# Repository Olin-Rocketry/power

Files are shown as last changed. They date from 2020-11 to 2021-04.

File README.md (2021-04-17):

# Power

## Current Design 
**Two independent groups of 3 cells in series.** <br>
**Nominal voltage: 12.3V**  <br>
**Nominal current: 4000 mAh** <br>

### The 25R 18650 Li-ion Battery
- Discharge rate: 2000 mA
- Range of voltage: 3.6V (EoD) - 4.1V (EoC)
- Current rating: 2500mAh
- Max voltage (switch from CV to CC):  4.1V
- Icc (charging current) = .25 A 
- Max cycle life: 100 cycles  
- Normal capacity: 80% (assumed) 
- Temperature range: -20 - 50 C

## System Diagram 
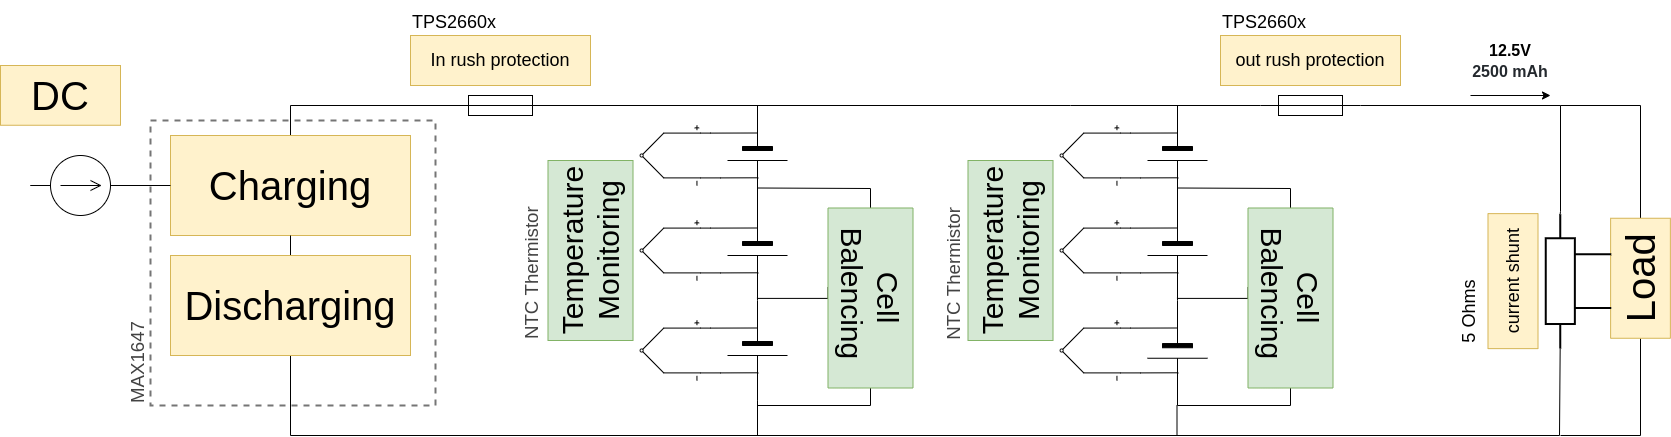
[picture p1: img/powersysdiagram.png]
bms_system_diagram


## Power Distribution
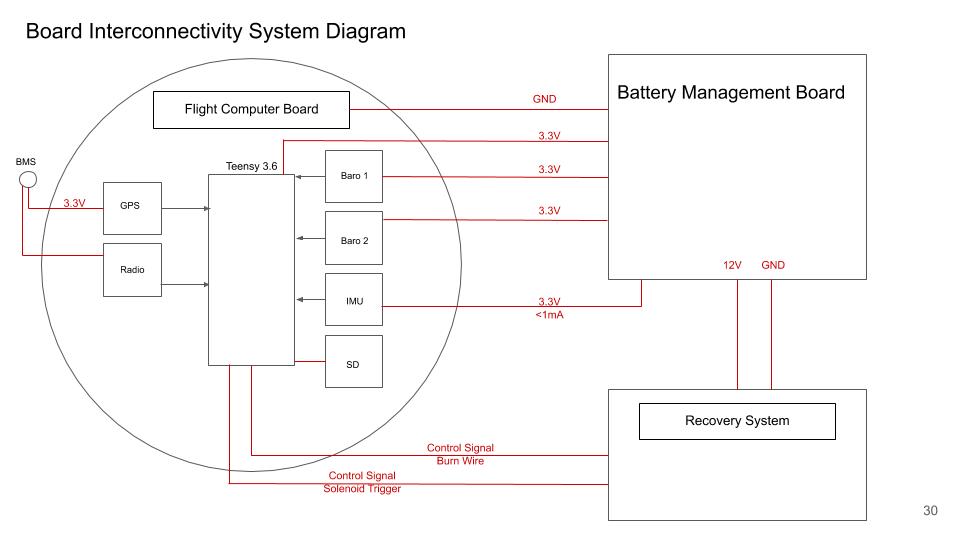
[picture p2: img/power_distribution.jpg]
power distribution


## Rev1 Schematic *1/2021
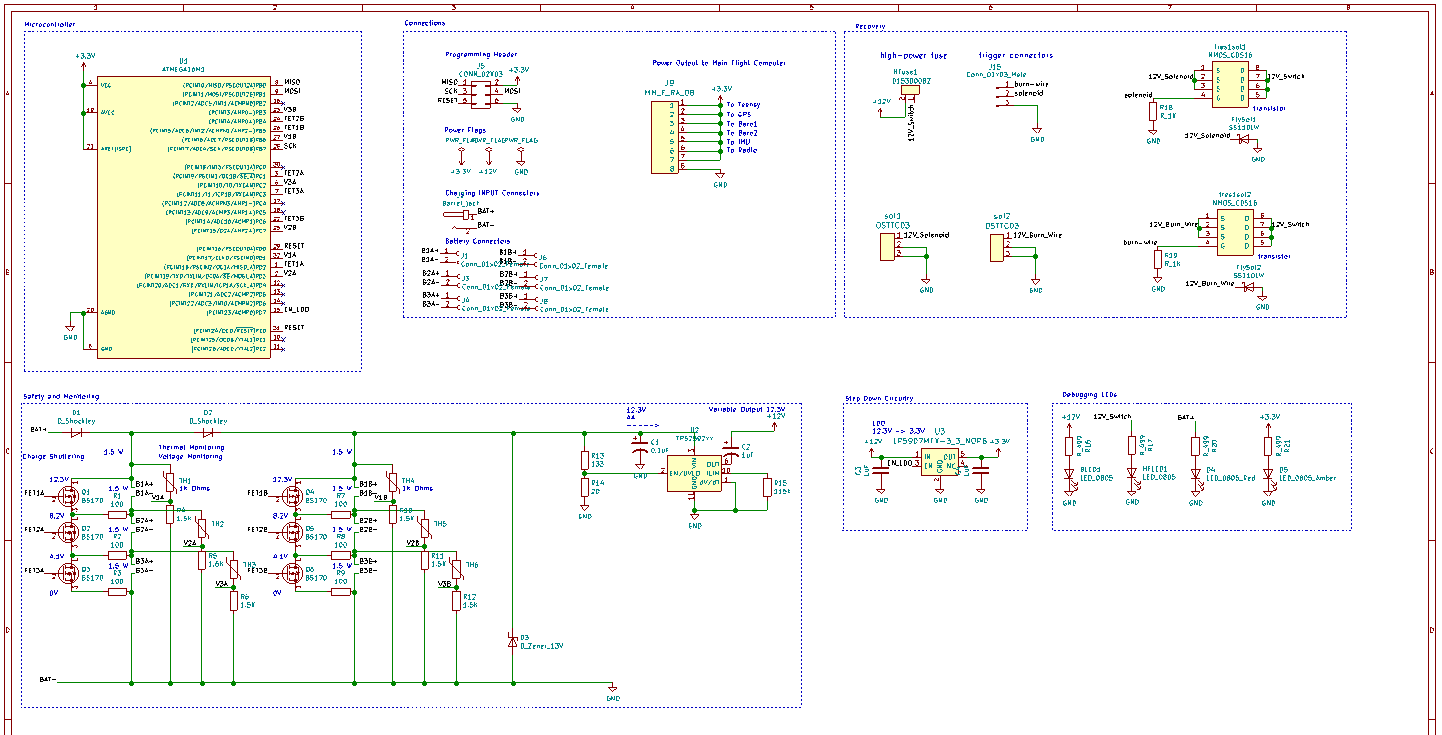
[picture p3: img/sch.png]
rev1_sch


## Rev1 PCB Layout and 3D Model *1/2021
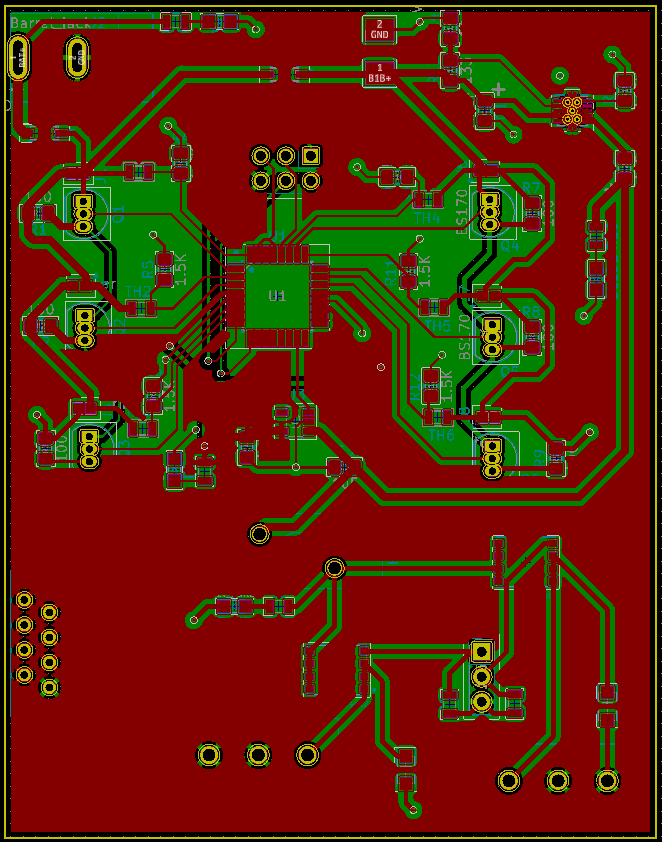
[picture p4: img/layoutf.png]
rev1_layout
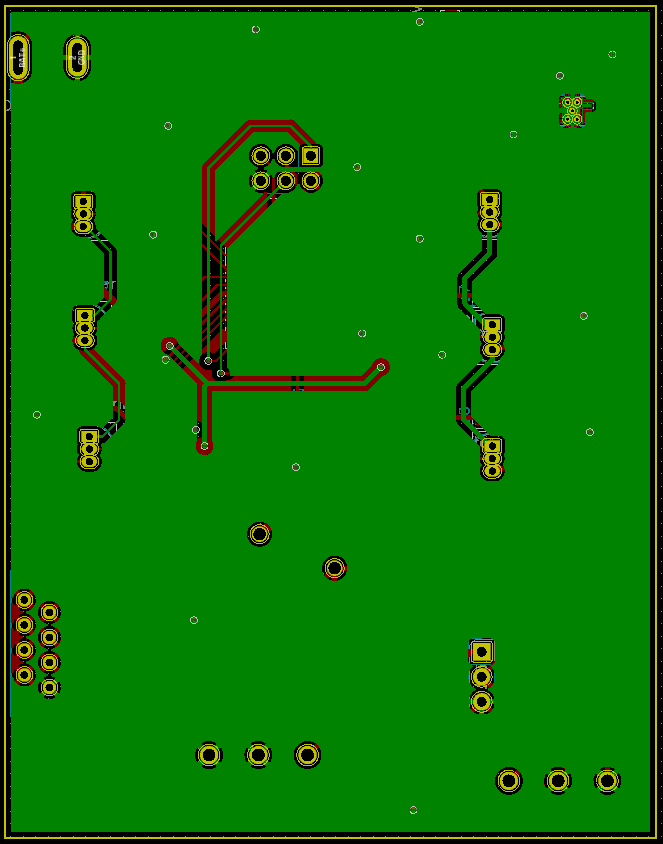
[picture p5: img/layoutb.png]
rev1_layoutb
 
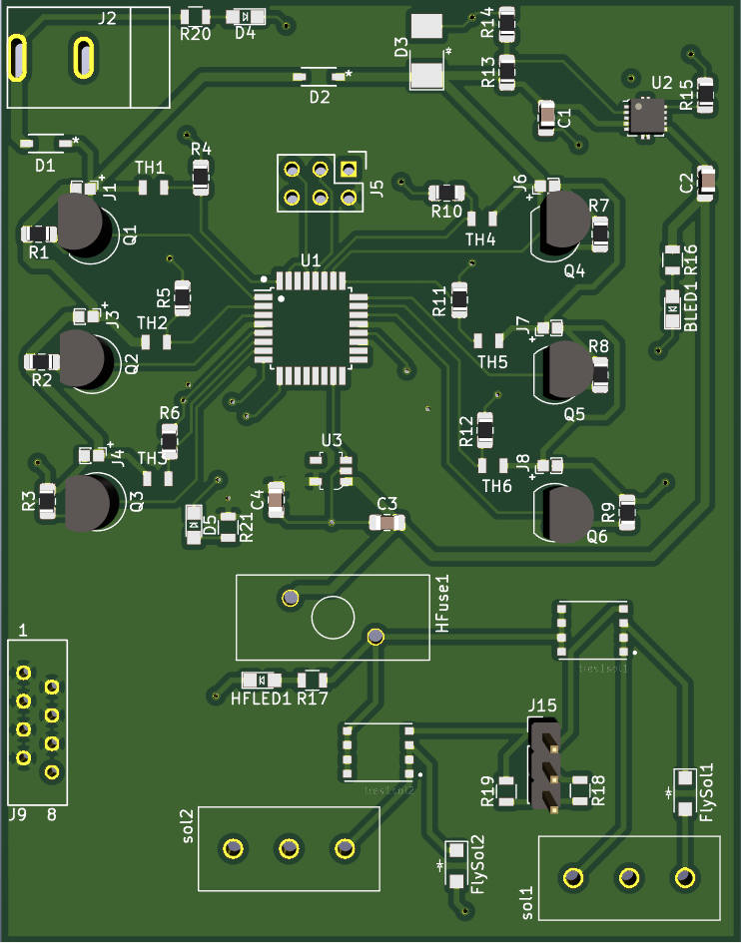
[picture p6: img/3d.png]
rev1_3d


### Subsystem loads 
| Subsystem | Voltage | Current |
|---|---|---|
| Solenoid  |  12.3V  |  880mA  |
| GPS |  3.3V |  30mA |  
| Radio |  3.3V |  50mA *at 13dBm* |
| Flight Computer | 3.3V | |
| BMS | 5V | |

(Live Power Budget Sheet)[https://docs.google.com/spreadsheets/d/1nH3F-o1HZTds1WetEKFTd1lCUxuCh-wOJmA-jhke28s/edit?usp=sharing]

## Firmware 
### MVP
- Read temperature from thermistors 
- Read voltage level of each battery 
- Calculate current flowing out of each battery 

### Goal 
- Trigger safety break of line when temperature rating or voltage level is above threshold 
- Balance cells using voltage readings 
- Display voltage levels 
- Send data via MQTT (or save data to SD)

## Requirements 
[General Rules and Reqs 2019](http://www.soundingrocket.org/uploads/9/0/6/4/9064598/sa_cup_irec_rules___requirements_document_20191118__rev_d_final_.pdf)
[Design, Test, Eval Guide 2019](http://www.soundingrocket.org/uploads/9/0/6/4/9064598/sa_cup_irec-design_test___evaluation_guide_20191118__rev_c_final_.pdf)
 
| Req. ID | Requirement | Implementation | Type |
|---|---|---|---|
|BAT_REQ_04 | Battery Life | The batteries shall provide at least 2500 mAh of charge to the non-COTS computer power flow | Team |
|BAT_REQ_05 | Battery Quantity | The battery management board shall manage two separate batteries | Team |
|BAT_REQ_06	| Battery Draw | The battery management board shall be able to supply an expected maximum of 2000 mA | Team |
|BAT_REQ_07	| Maximum Power | Draw	The battery management board shall not draw more than 250 mA during the mission| Team|
|BAT_REQ_08	| Overall Power | Draw	The battery management board shall not draw more than 100 mAh over the course of the mission |Team|

## Design Reviews 

[Design Review 1](https://docs.google.com/presentation/d/1L4w887s7x08WpU703jKznQMGognrjYOtB8_F7KaSsSU/edit?usp=sharing): Initial design validation for cell balancing, charging, and discharging *12/2019

[Design Review 2](https://docs.google.com/presentation/d/1s-o9i7a22b9S89c6PrSgXXXy9AWuLc9d6yVl3I3lAEo/edit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): Process design review touching on integration of ATMEGA, safety switches, and voltage distribution/regulation *12/2020

## Rev 2 Plans 
- USB input 
- Power supply input 
- Lin Reg for power input 
- 10k pull up resistor on RESET of Atmega16 
- Switch to non-smd or ATMEGA328
- Voltage difference monitored instead of direct analog to avoid 5.5V maximum

## Ordering PCBs From JLCPCB

For ordering the boards, go to JLCPCB.com, and click on "Quote Now" button.

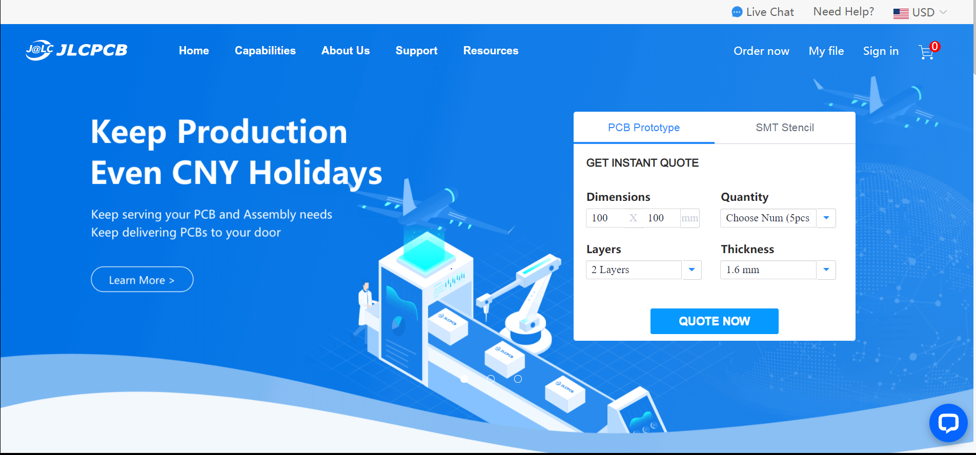
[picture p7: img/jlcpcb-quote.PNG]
jlcpcb quote


JLCPCB (ShenzhenJLC Electronics Co., Ltd.), is the largest PCB prototype enterprise in China, and a high-tech manufacturer specializing in quick PCB prototype and small-batch PCB production. You can order a minimum of 5 PCBs for just $2.

First: Upload the gerber files for the board by clicking the "Add gerber file" button. You’ll notice a message at the bottom if the file is successfully uploaded.

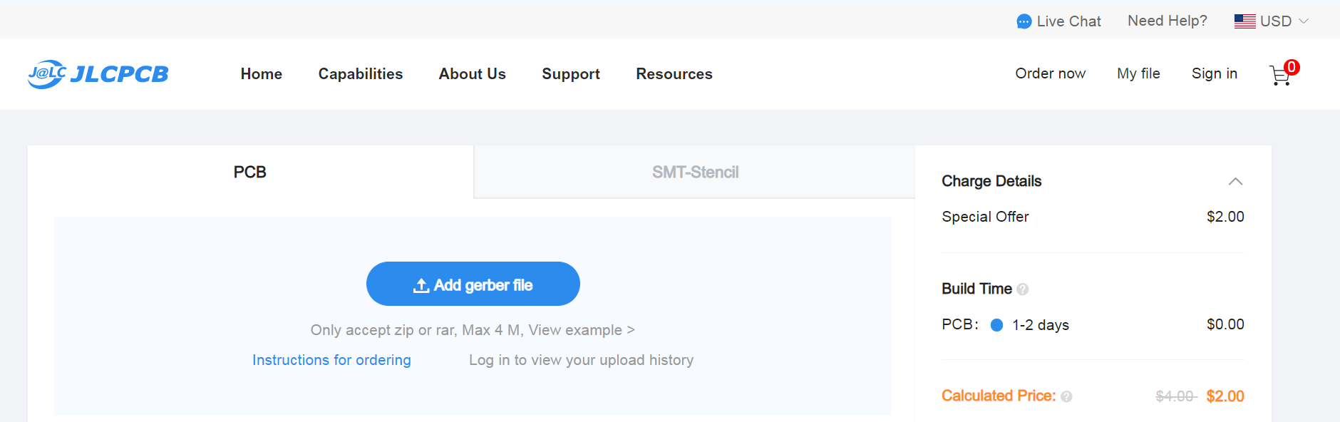
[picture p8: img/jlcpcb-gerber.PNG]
jlcpbc gerber


A correctly uploaded gerber folder renders the board as follows:

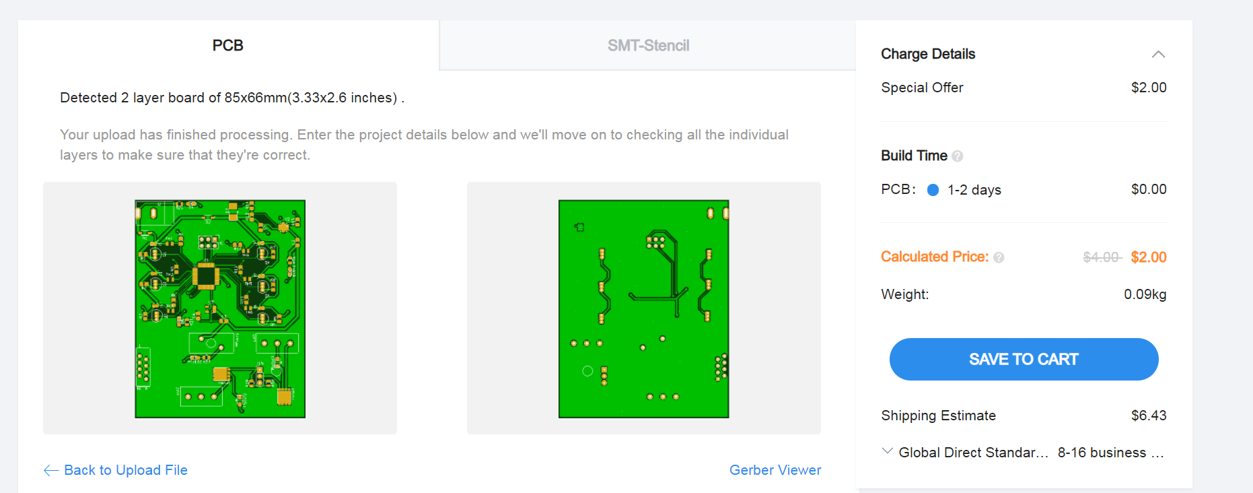
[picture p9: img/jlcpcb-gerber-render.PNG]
jlcpcb render


Second: In order to get the board assembled (optional, based on the project requirements), select the "SMT Assembly option. It is important to select the side of the PCB that needs to be assembled, as well as the quantity for SMT. Press the "Confirm" button, then press the "Next" button.

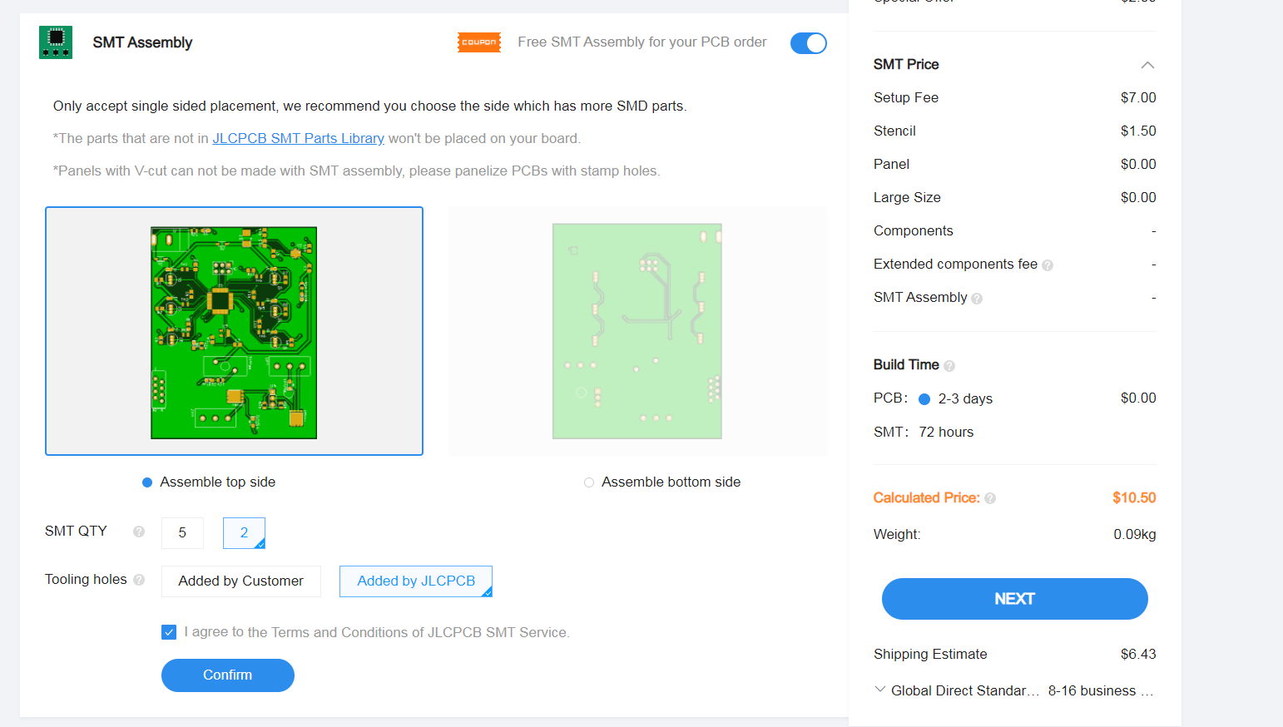
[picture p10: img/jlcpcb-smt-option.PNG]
jlcpcb smt


Third: upload the BOM (Bill of Material) and CPL (Component Placement List) files and click the "Next" button. It is necessary to make sure that each of these files follow the jlcpcb specified BOM and CPL formats, respectively:
* [Sample BOM](https://jlcpcb.com//video/JLCSMT_Sample_BOM1.xlsx?_ga=2.42560357.1905056644.1612161700-100444678.1610257845)
* [Sample CPL](https://jlcpcb.com//video/JLCSMT_Sample_CPL1.xlsx?_ga=2.42560357.1905056644.1612161700-100444678.1610257845)
* [SMT FAQ's](https://support.jlcpcb.com/category/78-smt-assembly?_ga=2.42560357.1905056644.1612161700-100444678.1610257845)

Note: If there is an issue with the BOM/CPL formatting, the the page will keep erroring out until it is resolved.

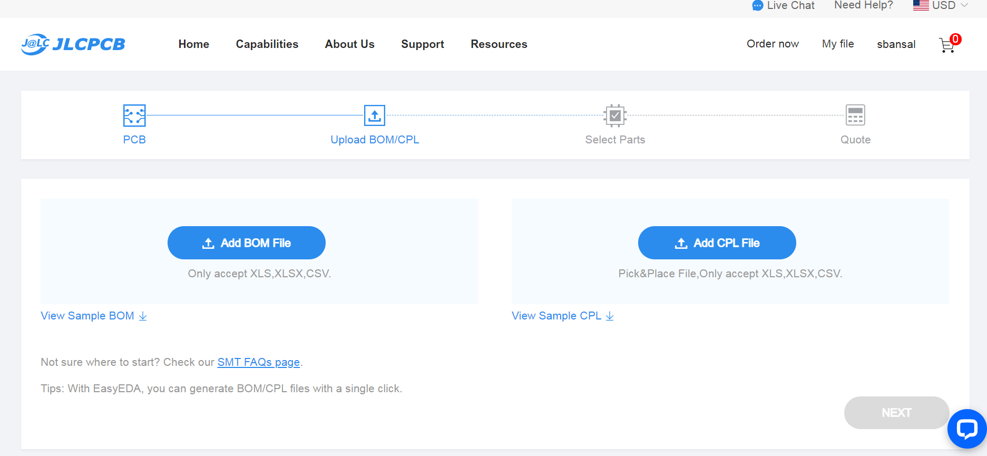
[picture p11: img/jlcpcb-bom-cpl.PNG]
jlcpcb bom


Fourth: The parts are automatically detected through the uploaded BOM. They are also matched against jlcpcb's in-stock parts. It is important to go through each row and confirm if the auto-detected parts are the desired parts. Some parts will remain undetected if they cannot be assembled through SMT and require manual assembly post-deilvery.

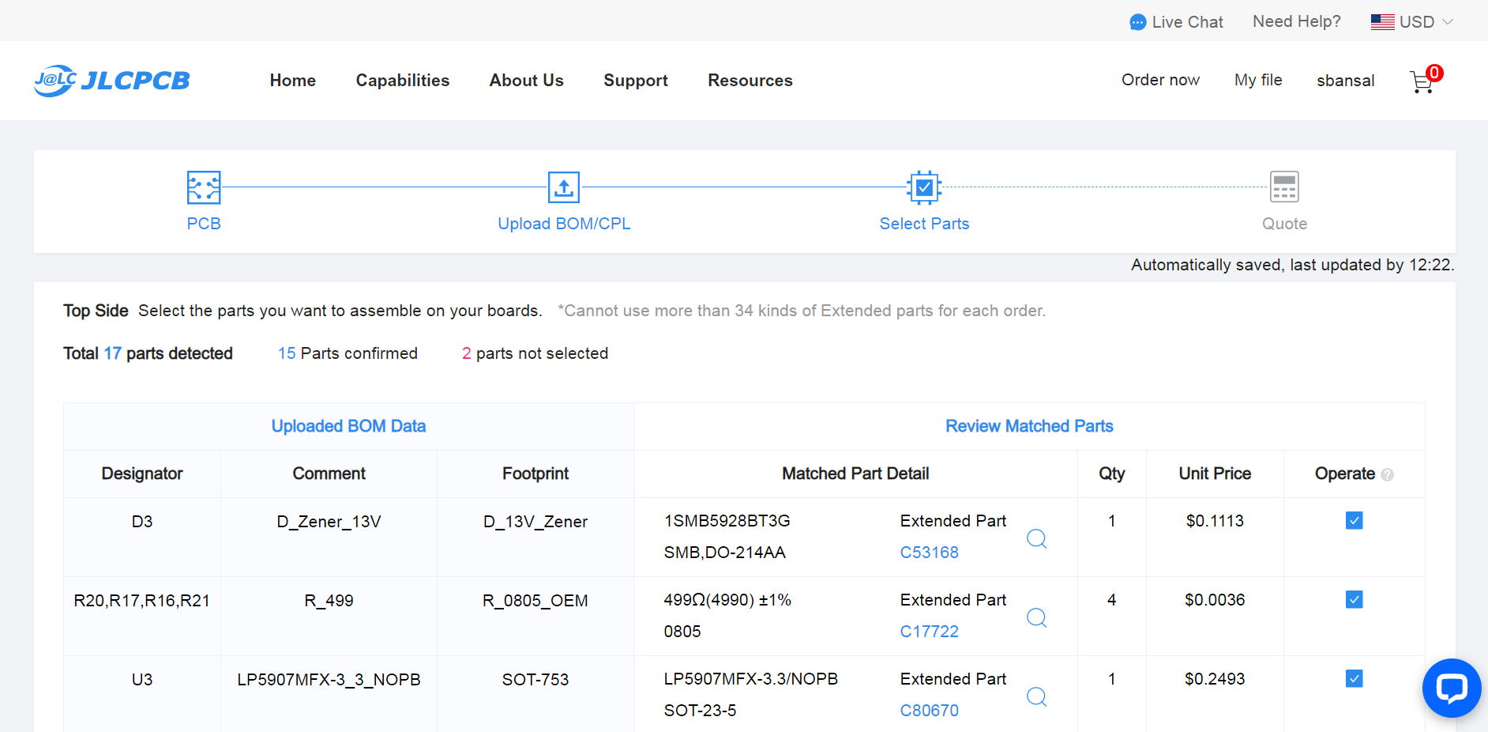
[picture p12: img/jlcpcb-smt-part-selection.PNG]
jlcpcb parts


Fifth: The website renders an assembled board using the CPL file. This feature can be used to review the placement of the components (including orientation). Once carefull reviewed, the next step is to download a list of parts remaining to be assembled towards the bottom of this page view. It is important to place an order for the remaining components to be manually assembled upon delivery. 

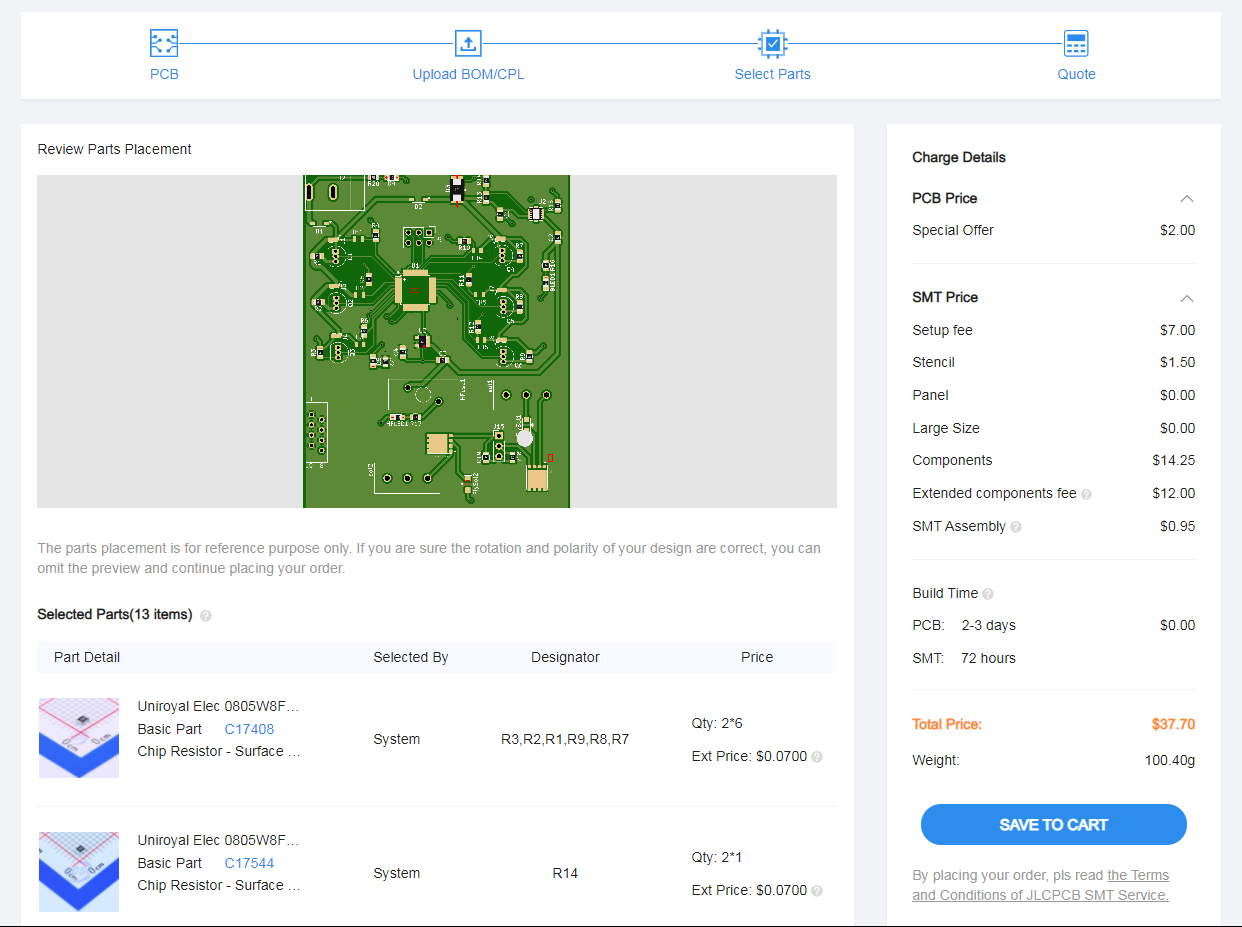
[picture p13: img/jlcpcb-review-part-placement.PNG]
jlcpcb review


Sixth: Click on the “Save to Cart” button. Then, click on the "Secure Checkout" button. 

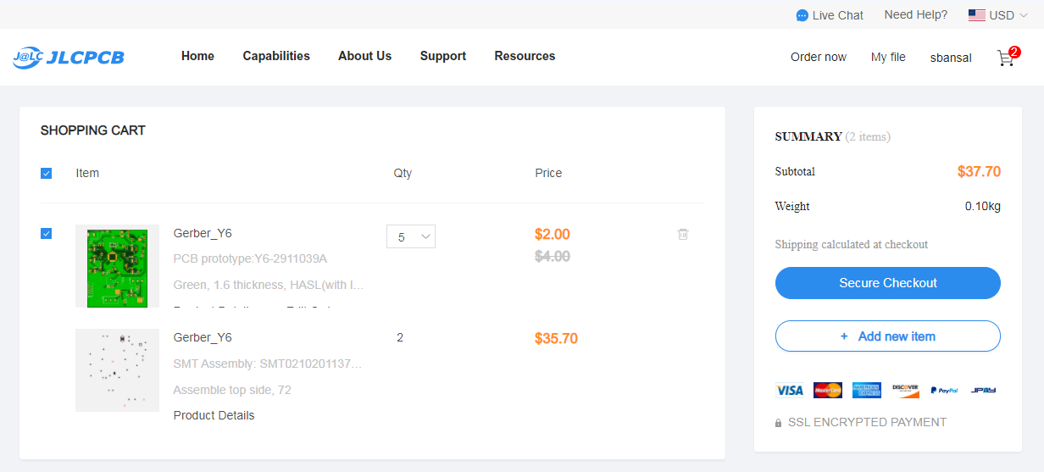
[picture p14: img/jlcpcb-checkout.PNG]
jlcpcb checkout


Last: Add the payment details and choose the suitable delivery method (this includes FedEx, DHL, and standard mail options). Then, place the order.

Optional: To review the production status of the board, click on the "Order History" button under username. Then, click on In Production > view progress to obtain timestamps for each of the production steps in real time. 

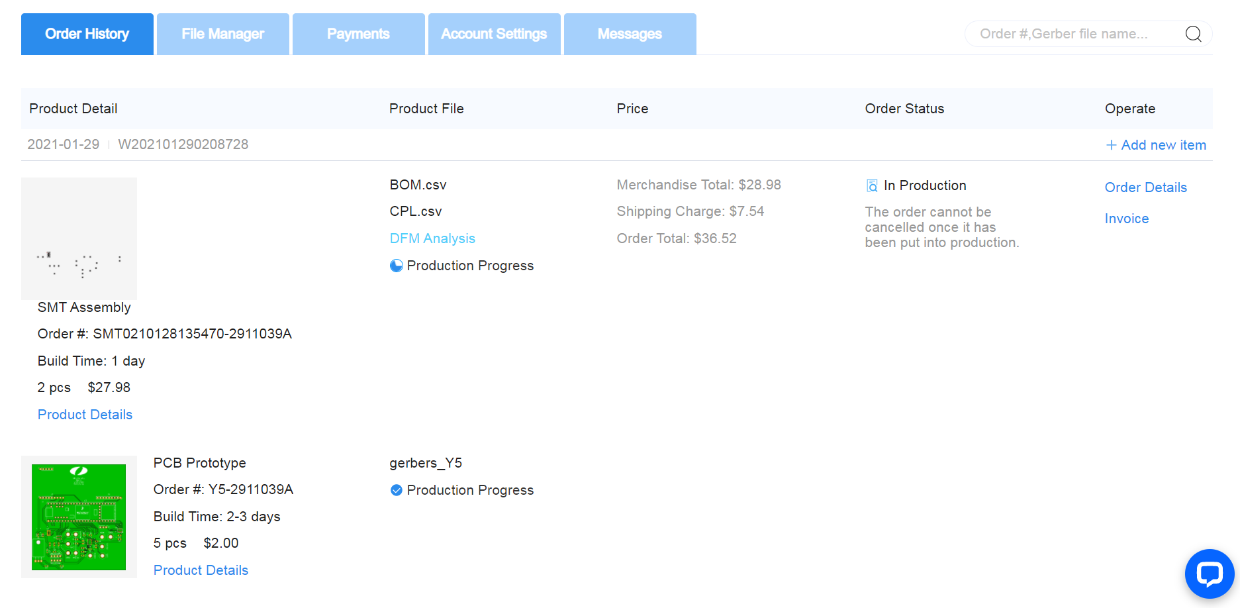
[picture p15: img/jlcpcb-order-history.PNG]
jlcpcb production


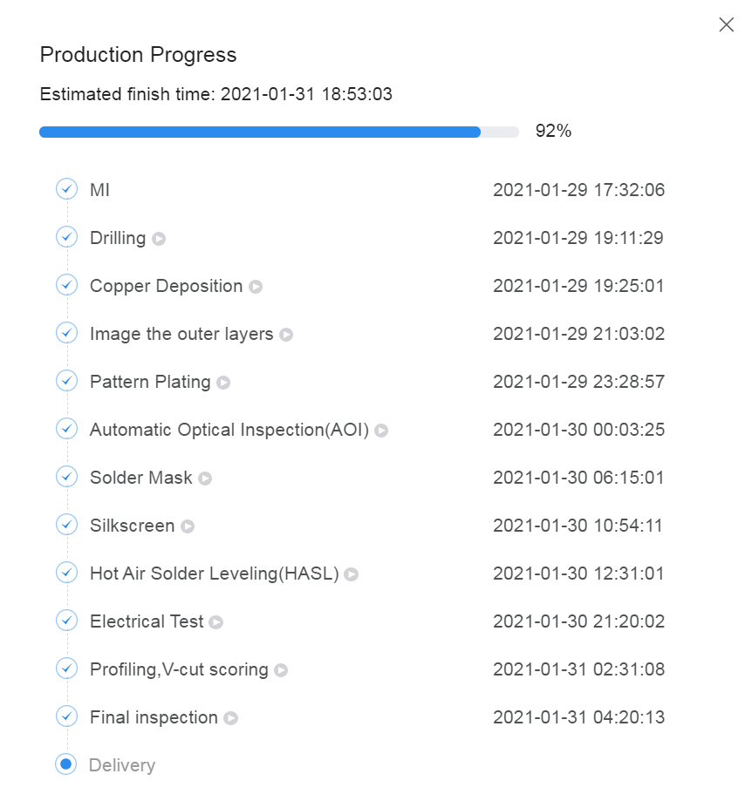
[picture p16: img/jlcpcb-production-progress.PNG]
jlcpcb production progress


## Questions and Considerations

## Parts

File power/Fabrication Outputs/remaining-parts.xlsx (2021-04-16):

Designator | Comment | Footprint | Quantity | Vendor
FLYSOL2,FLYSOL1 | SS110LW | D_SOD-123W_OEM | 2 | Digikey | https://www.digikey.ch/product-detail/en/taiwan-semiconductor-corporation/SS110LW-RVG/SS110LWRVGCT-ND/7359346
U1 | ATMEGA16M1 | TQFP-32_7X7MM_PITCH0.8MM | 1 | Digikey
J5 | CONN_02X03 | PIN_HEADER_STRAIGHT_2X03 | 0 | Digikey
J15 | CONN_01X03_MALE | PINHEADER_1X03_P2.54MM_VERTICAL | 0 | Digikey
J2 | BARREL_JACK | BARREL_JACK_PJ-037A | 0 | Digikey
 |  |  |  | Digikey
J9 | MM_F_RA_08 | MICROMATCH_FEMALE_RA_8 | 0 | Digikey
HFUSE1 | 01530008Z | 01530008Z | 0 | Digikey
TH4,TH6,TH5,TH3,TH2,TH1 | THERMISTOR | THERMISTOR | 0 | Digikey
D2,D1 | D_SHOCKLEY | SD103AW-13-F | 0
SOL1,SOL2 | OSTTC03 | OSTTC030162 | 0 | Digikey
Q5,Q4,Q3,Q2,Q1,Q6 | BS170 | TO-92_INLINE | 0
TRES1SOL1,TRES1SOL2 | NMOS_CDS16 | TRANS_CSD17312Q5 | 0 | Digikey

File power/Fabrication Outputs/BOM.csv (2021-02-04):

Comment | Designator | Footprint
NMOS_CDS16 | tres1sol1,tres1sol2 | TRANS_CSD17312Q5
Conn_01x02_Female | J6,J1,J3,J4,J7,J8 | nickle_pads_1x2
1.5K | R5,R6,R4,R12,R11,R10 | R_0805_2012Metric_Pad1.15x1.40mm_HandSolder
R_499 | R20,R17,R16,R21 | R_0805_OEM
R_1K | R19,R18 | R_0805_OEM
Conn_01x03_Male | J15 | PinHeader_1x03_P2.54mm_Vertical
CONN_02X03 | J5 | Pin_Header_Straight_2x03
LP5907MFX-3_3_NOPB | U3 | SOT-753
BS170 | Q5,Q4,Q3,Q2,Q1,Q6 | TO-92_Inline
ATMEGA16M1 | U1 | TQFP-32_7x7mm_Pitch0.8mm
Thermistor | TH4,TH6,TH5,TH3,TH2,TH1 | Thermistor
115K | R15 | R_0805_2012Metric_Pad1.15x1.40mm_HandSolder
133 | R13 | R_0805_2012Metric_Pad1.15x1.40mm_HandSolder
100 | R3,R2,R1,R9,R8,R7 | R_0805_2012Metric_Pad1.15x1.40mm_HandSolder
01530008Z | HFuse1 | 01530008Z
LED_0805 | HFLED1,BLED1 | LED_0805_OEM
SS110LW | FlySol2,FlySol1 | D_SOD-123W_OEM
LED_0805_Amber | D5 | LED_0805_OEM
LED_0805_Red | D4 | LED_0805_OEM
1uF | C4,C3,C2 | C_0805_2012Metric_Pad1.15x1.40mm_HandSolder
D_Zener_13V | D3 | D_13V_Zener
Barrel_jack | J2 | barrel_jack_PJ-037A
D_Shockley | D2,D1 | SD103AW-13-F
20 | R14 | R_0805_2012Metric_Pad1.15x1.40mm_HandSolder
0.1uF | C1 | C_0805_2012Metric_Pad1.15x1.40mm_HandSolder
OSTTC03 | sol1,sol2 | OSTTC030162
MM_F_RA_08 | J9 | micromatch_female_ra_8
TPS2592xx | U2 | VSON-10-1EP_3x3mm_P0.5mm_EP1.65x2.4mm_ThermalVias

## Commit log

2020-10-02 Outline of power readme
2020-10-08 updated power specs
2020-10-08 reqs docs and battery table
2020-10-30 Updated Schematic and System Diagram
    [power.kicad_pcb, power.sch]
2020-11-21 power diagram
2020-11-23 added to sch
    [power.sch]
2020-11-23 added system diagram and power distribution
2020-11-23 Added proper power budgets
2020-11-23 changed to atmega16
    [power.sch]
2020-12-01 Proper atmega configuration with programming header pins
    [power.sch]
2020-12-05 negative terminals of bat
    [power.sch]
2020-12-08 wattage and values for charging circuit
    [power.sch]
2020-12-08 bleeding resistor values and wattage, discharging current sink circuit complete
    [power.sch]
2020-12-09 buck converters added and LDO added
    [power.sch]
2020-12-26 complete schematic
    [power.sch]
2020-12-28 rev 2 copy for bq76930 ic
    [_saved_power_rev2.sch, power_rev2.kicad_pcb, power_rev2.sch]
2020-12-28 balancing with bq rev 2
    [power_rev2.sch]
2020-12-28 rev1 layout organization
    [power.sch, power_rev2.sch]
2020-12-30 thermistor footprint
    [power.kicad_pcb, power.sch]
2020-12-31 removed extra thermistor
    [power.sch]
2021-01-01 separated charging from main board
    [charging.kicad_pcb, charging.sch, noname.sch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]
2021-01-03 half layout
    [power.kicad_pcb, power.sch]
2021-01-03 complete layout
    [power.kicad_pcb, power.sch]
2021-01-05 power traces increased to 0.8
    [power.kicad_pcb]
2021-01-05 generated bom and gerber files
    [power.csv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]
2021-01-06 debugging LEDs, recovery
    [power.sch]
2021-01-07 layout complete other than missing recovery footprints
    [power.kicad_pcb, power.sch]
2021-01-11 final rev 1: nickel pads added and recovery footprint issues fixed
    [power.csv, power.kicad_pcb, power.sch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]
2021-01-12 ribbon added to sch and recovery wires increased and no connects added
    [power.kicad_pcb, power.sch]
2021-01-14 complete bms - 0 drc errors, ribbon cable, pads not on edge
    [power.kicad_pcb, power.sch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]
2021-01-16 gerber folder
    [power.csv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]
2021-01-16 cpl generation in /gerber
    [power-bottom-pos.csv, power-top-pos.csv]
2021-01-16 BOM attempt 100000
    [output.csv]
2021-01-16 BOM generation attempt 10000001
    [output.csv]
2021-01-16 if this doesn't work, jlcpcb can die
    [BOM.csv, output.csv, power.csv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]
2021-01-16 Update CPL
    [power-top-pos.csv]
2021-01-16 Add remaining parts list
    [output.xlsx, remaining-parts.xlsx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]
2021-01-18 Add new gerbers
    [BOM.csv, output.xlsx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]
2021-01-19 complete bms with list checked
    [_saved_power.sch, power.kicad_pcb]
2021-01-22 final power
    [power.sch]
2021-01-22 complete jlc BOM and CPL and GERBER
    [BOM.csv, kicadbom.csv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]
2021-01-22 comma separation
    [BOM.csv]
2021-01-22 Fix U3 orientation
    [CPL.csv]
2021-01-28 updated purchasing links
    [power.sch]
2021-02-01 Add PCB order procedure
2021-04-17 added 10K on reset, power conditional setup for testing rev2
    [power.sch]
